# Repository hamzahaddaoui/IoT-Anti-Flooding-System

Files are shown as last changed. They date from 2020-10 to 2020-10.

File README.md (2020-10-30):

# IoT Anti flooding

The designed anti-flooding system has the task of constantly monitoring certain parameters within a room where tests are carried out on coffee machines.
7 anti-flood sensors have been used, 5 mounted under each coffee machine, and 2 below the delivery pipe.
Furthermore, there is a pressure switch, in charge of measuring the water pressure and a volumetric meter, measuring the current water consumption. 
The system has the task of interrupting, through two solenoid valves, the water flow when one or more anomalies occur, including:
• Decrease in water pressure
• High water consumption
• Detection of water leaks (via flood sensors)
The sensors and devices are monitored via an electronic board (or via an electronic board by removing one) and, in the event of an anomaly, the two solenoid valves can also be deactivated by the board itself.
The control unit also sends the data related to each single sensor to a server, in order to be able to carry out a remote control. It is possible to check in any moment the situation of the system, and perform some actions.

### Board


### Electronics schematic



### Electrical schematic



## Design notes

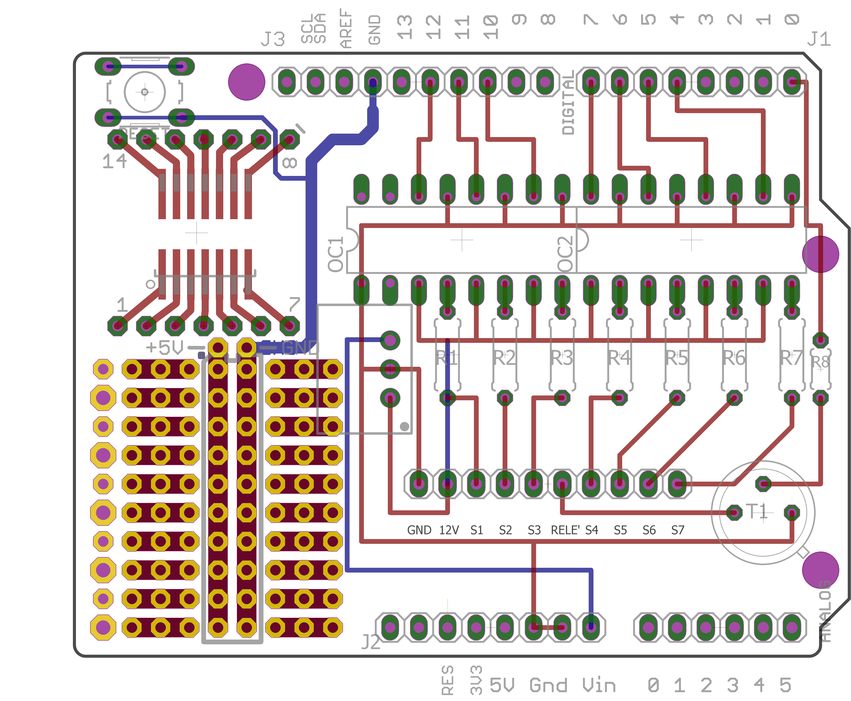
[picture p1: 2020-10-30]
documentation/ProtoShield_PCB.png

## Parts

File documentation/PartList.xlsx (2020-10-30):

SISTEMA ANTI ALLAGAMENTO
Lista componenti
No. | Descrizione | Modello | Specifiche tecniche | Produttore | Q.tà
1 | Bobina per valvole a solenoide | IM21M | 220Vac 50/60Hz | Fantini Cosmi | 1
2 | Corpo valvola a solenoide | M23D13 | G 1/2" | Fantini Cosmi | 1
3 | Interruttore elettro-magnetico | IC60H | 10A max , 220/240 Vca, 2 poli | Schneider Electric | 1
4 | Alimentatore 12Vdc | MDR-20-12 | Output 12Vdc, 1.67A max | Mean Well | 1
5 | Sensore di allagamento | FGFS-101 | 12Vdc-24Vdc | Fibaro System | 1
6 | Sensore di allagamento | LD-12 | 12Vdc | Jablotron Alarms | 5
7 | Relè monostabile NO + Socket | 2901873 | 12Vdc, 10mA | Phoenix Contact | 7
8 | Relè di potenza | Finder 55.34.9.012 | 240/400Vac, 7A, 4 contatti | Finder | 1
9 | Contatore Volumetrico | - | - | - | 1
10 | Pressostato | - | - | - | 1
11 | Elettrovalvola | - | - | - | 2
12 | Scheda di sviluppo software | FRDM-K64F | - | Freescale | 1
13 | ProtoShield | Arduino ProtoShield | - | Arduino | 1
14 | Optoisolatori | TLP521-4 | Imin Led = 16mA, 1.15V drop | Toshiba | 2
15 | Transistor | BC302 | NPN, hFE min = 40 | CDIL | 1
16 | DC/DC converter | 173950578 | 6-28v IN, 5v 500mA OUT | Wurth Electronik | 1
17 | Morsettiera | - | 10poli | - | 1
18 | Resistori | - | 7x 10K , 1x 3K3 | - | 8

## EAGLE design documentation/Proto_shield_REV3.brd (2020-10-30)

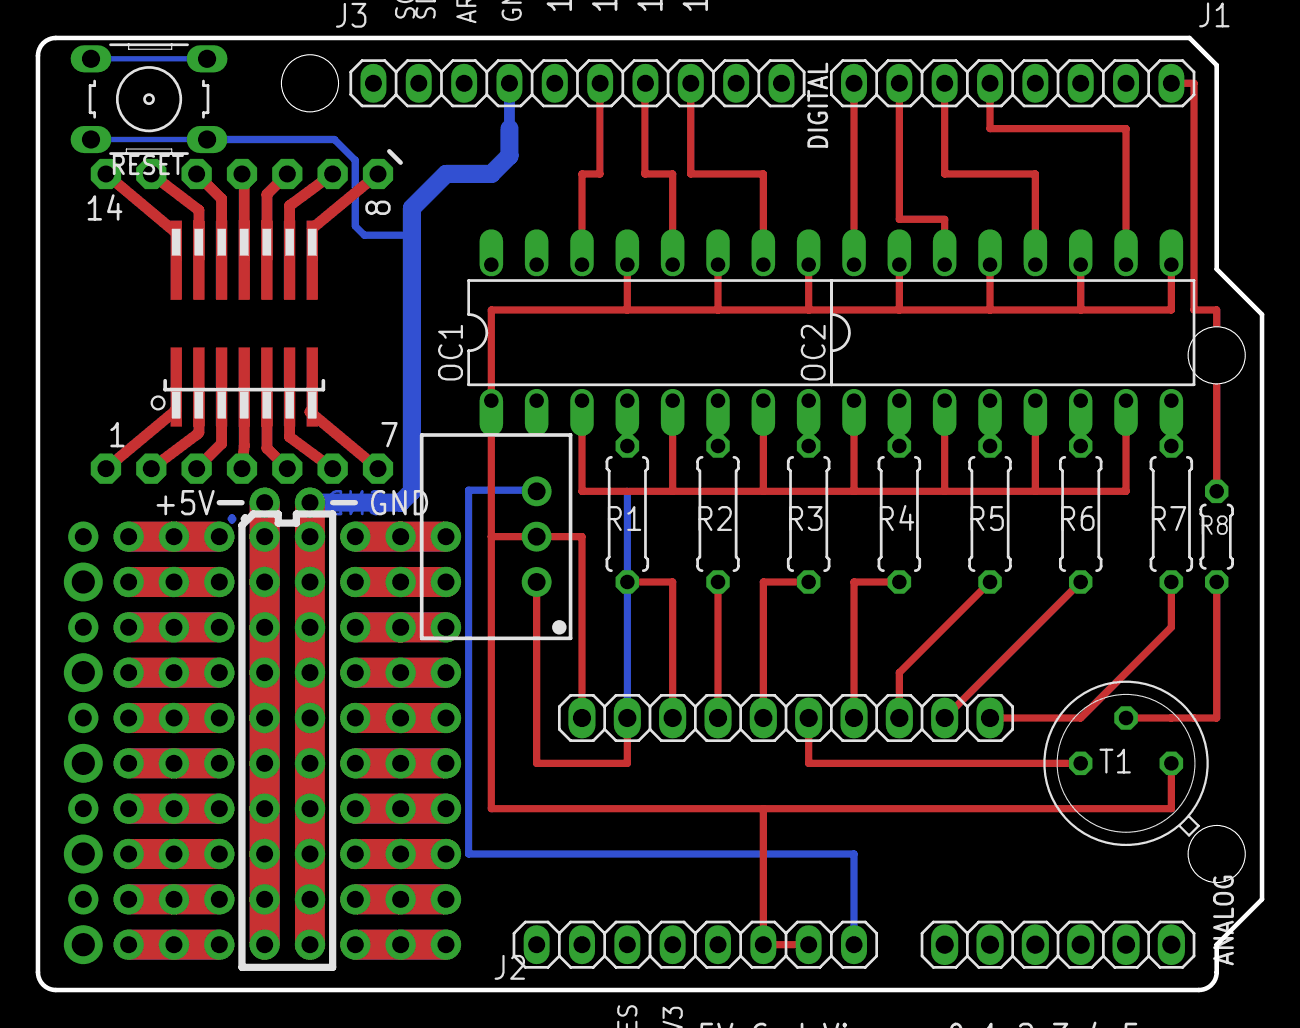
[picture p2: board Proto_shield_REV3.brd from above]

Board: 2 copper layers, 68.6 x 53.3 mm, 33 parts (0 on the bottom side), 40 nets.

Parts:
1, 2, 3, 4, 5, 6, 7, 8, 9, 10, 11, 12, 13, 14: LSP10
12V/5V: SIP3
ANALOG: 1X06
E$13: 1X10
IC2: SMD-14; SO-14NMW
J1, J2: 1X08-TH
J3: 1X10-TH
OC1, OC2: DIL16
R1, R2: 10K x 7; 0207/7
R3, R4, R5, R6, R7: 10K; 0207/7
R8: 0204/5
RESET: B3F-10XX
T1: TO5

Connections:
GND: 12V/5V.2, E$13.1, J2.7, OC1.9, OC1.11, OC1.13, OC2.9, OC2.11, OC2.13, OC2.15, T1.1
unnamed: 14.MP, IC2.P$14
unnamed: 13.MP, IC2.P$13
unnamed: 12.MP, IC2.P$12
unnamed: 11.MP, IC2.P$11
unnamed: 10.MP, IC2.P$10
unnamed: 9.MP, IC2.P$9
unnamed: 8.MP, IC2.P$8
unnamed: 7.MP, IC2.P$7
unnamed: 6.MP, IC2.P$6
unnamed: 5.MP, IC2.P$5
unnamed: 3.MP, IC2.P$3
unnamed: 2.MP, IC2.P$2
unnamed: 1.MP, IC2.P$1
unnamed: 4.MP, IC2.P$4
S$2: OC2.8, R7.2
S$3: OC1.4, R1.2
S$4: OC1.6, R2.2
S$5: OC1.8, R3.2
S$6: OC2.2, R4.2
S$7: OC2.4, R5.2
S$8: OC2.6, R6.2
S$9: OC1.3, OC1.5, OC1.7, OC2.1, OC2.3, OC2.5, OC2.7
S$10: E$13.6, T1.3
S$11: J3.7, RESET.1, RESET.2
S$12: E$13.3, R1.1
S$13: E$13.10, R7.1
S$14: RESET.3, RESET.4
S$15: 12V/5V.1, E$13.2
S$16: E$13.4, R2.1
S$17: E$13.5, R3.1
S$19: J1.1, R8.2
S$20: R8.1, T1.2
S$23: J1.8, OC2.16
S$24: J1.7, OC2.14
S$25: E$13.7, R4.1
S$26: E$13.8, R5.1
S$27: E$13.9, R6.1
S$29: J1.6, OC2.12
S$30: J1.5, OC2.10

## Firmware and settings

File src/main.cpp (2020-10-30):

#include "mbed.h"
#include "EthernetInterface.h"
#include "HTTPClient.h"

//MACRO
#define ethSendData 10           //RITARDO TRA UN INVIO AL SERVER E L'ALTRO
#define contVolumTime 100       //TEMPO MIN TRA UN IMPULSO E L'ALTRO (CONTATORE VOLUMETRICO)
#define pressoTime 2            //TEMPORIZZATORE PRESSOSTATO

//ETHERNET CONFIG
EthernetInterface eth;
HTTPClient http;
char str[2048], ret;
char key[9][5] = {"s1","s2", "s3", "s4", "s5", "s6", "s7", "s8", "s9"};

//CONFIG input/output
DigitalIn reset(SW2);

BusIn sensori(D4,D5,D6,D7,D10,D11,D12);

InterruptIn sensVolumetrico(D1);  
DigitalIn contVolumetrico(D1);    
 
InterruptIn sensPressione(D2);
DigitalIn pressostato(D2);

DigitalOut relay(D0);          
DigitalOut greenLed(LED_GREEN);
DigitalOut redLed(LED_RED);

//TIMER E INTERRUPT TIMER
Timer contatore;                                    //TIMER per contare il tempo tra un impulso e l'altro del contatore volumetrico
Timer contatoreEth;                                 //timer per Ethernet
Timeout temporizzatore;                             //TIMEOUT per "temporizzare" il pressostato
Timeout temporizzatore2;                            //TIMEOUT per contatore volumetrico. Se in allarme, dopo 100 secondi verifico nuovamente lo stato del contatore

//VARIABILI GLOBALI
unsigned char i;
bool alarm[9];                                      //ARRAY ALLARMI PER OGNI SORGENTE
unsigned char allarme;                                      //ALLARME GENERICo
unsigned int tempo=contVolumTime,n=0;
bool status=0;

//FUNZIONI
void setup();
void controlloConsumo();
void controlloPressione();

void setup(){ 
    sensVolumetrico.rise(&controlloConsumo);
    sensPressione.rise(&controlloPressione);
    sensPressione.fall(&controlloPressione);
    sensori.mode(PullUp);                         //PULL-UP IN VERSIONE DEFINITIVA
    sensVolumetrico.mode(PullUp);                 //ok
    sensPressione.mode(PullUp);                  //Ok
    contatore.start();
    contatoreEth.start();
    allarme=0;
    printf("SYSTEM STARTED\n");
}
int main(){
    eth.init(); //Use DHCP
    eth.connect();
    HTTPMap map;
    map.clear();
    HTTPText inText(str, 2048);
    setup();
    while(1){
        map.clear();
        for(i=0;i<7;i++){
            alarm[i]=sensori[i].read();
        }
        for(i=0;i<9;i++){               //controllo allarmi 
            if (alarm[i]==1) allarme=1;
        }   
        if (contatoreEth.read() >= ethSendData){       //invio dati al server
            for(i=0;i<9;i++){               // creazione map e stampa seriale
                if (alarm[i]==1){ 
                    map.put(key[i],"true");
                    printf("%s: true\n",key[i]);
                }
                else{
                    map.put(key[i], "false");
                    printf("%s: false\n",key[i]);
                }
            }
            contatoreEth.reset();
            contatoreEth.start();
            printf("\nPost dati in corso...\n");
            ret = http.post("http://192.168.1.251:55555/itf/setsensorsparam", map, &inText);
            if (!ret){
                printf("POST eseguito con successo! - %d caratteri letti\n", strlen(str));
                //printf("Result: %s\n", str);
            }
            else{
                printf("Errore - Codice di errore = %d\n\n", http.getHTTPResponseCode());
            }
        }
        if (allarme==0 || reset==0){
            relay.write(1);
            greenLed.write(0);
            redLed.write(1);
            if (reset==0) {
                allarme=0;
                tempo=contVolumTime;
                alarm[7]=0; 
            }
        }
        else{
            relay.write(0); 
            greenLed.write(1);
            redLed.write(0);
        } 
    }
}

void controlloConsumo(){
    tempo += contatore.read();
    if (contVolumetrico.read()==1){
        if ((n*100)+tempo<contVolumTime){
            alarm[7] = 1;      
        }
        tempo=0;
        n=0;
    }
    else{
        alarm[7]=0;
        n=tempo/contVolumTime;
        tempo=tempo%contVolumTime;
    }
    temporizzatore2.detach();
    temporizzatore2.attach(&controlloConsumo,contVolumTime);
    contatore.reset();
}


void controlloPressione(){
    temporizzatore.detach();
    if (pressostato.read()==1 && status==0){
        temporizzatore.attach(controlloPressione,pressoTime);
        status = 1;
    }
    else if (pressostato.read()==1 && status==1){
        alarm[8]=1;   
    }
    else if (pressostato.read()==0){
        alarm[8]=0;
        status = 0;
    }
}
